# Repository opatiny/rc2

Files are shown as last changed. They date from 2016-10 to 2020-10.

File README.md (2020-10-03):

# Remote Control Cylinder

---
Link to "site": https://opatiny.github.io/rc2/.

__WARNING:__ This README is not the main source of information for this project. A detailled paper can be found [here](https://github.com/opatiny/rc2/blob/master/documentation/RemoteControlCylinder.pdf).

  

_Final cylinder prototype_

## Cite this repository

Océane Patiny, & Luc Patiny. (2020, October 3). opatiny/rc2: Remote controlled cylinder final documentation (Version v1.0.0). Zenodo. http://doi.org/10.5281/zenodo.4064763

## Abstract
This one year project consists in the development of a remote controlled cylinder that uses servo motors to displace its center of mass, which leads the cylinder to accelerate linearly. This implies that very diversified fields such as mathematics, physics, programming, electronics and mechanics had to be explored and partly understood to be combined in the final prototype. This prototype has an acrylic glass base structure with a diameter of 32 cm, it is controlled using a C.H.I.P. Pro (a micro-controller similar to Raspberry Pi) and a customized dedicated extension board. The board includes a driver for four servo motors and a 6 axis accelerometer. Finally, the power supply consists of a pack of three AA batteries. All the programming was made using JavaScript scripts that are run using Node.js and a Shell. In addition, the cylinder is remotely controlled through a web page, which make it easy and intuitive for the user. The final features of this robotic cylinder are the following: it can roll forwards and backwards, stop and keep itself balanced on a gentle slope . Also, it is only working well on flat, hard surfaces, though it could easily be adapted to rougher surfaces. The possibility has also been considered of creating a sphere that uses the same technologies as the cylinder that was constructed in this project. The results of the project can be seen easily in [this movie](https://youtu.be/QggOjoGjJhA).

## Liscence

Finally, this work is meant to be as open-source as possible. Therefore, the software that was developed is under MIT licence, whereas the hardware is under CERN OHL.

## Concept

Initially the project was inspired by a rover realized by [Octanis](https://www.octanis.org/), a student's association specialized in electronics. The rover was supposed to be send to Antarctica and be able to analyse it's environment autonomously. Seeing the Rover tested on a Glacier on a windy day made me wonder what would be the best design for a windproof robot and I immediately thought of a spherical robot. However, once I got back home and looked for similar ideas, I realized that they were already existing projects that consisted in a spherical robot. One of the most famous being the [Sphero](https://www.sphero.com/), a spherical robot toy.

Looking further, I also realized that most of the projects use a similar approach to move the sphere: I call it the hamster wheel approach. It basically is a little car which wheels lay on the outer, rigid shell that induces the movement. I, on the contrary, had imagined a completely different system: I would displace the center of mass of the cylinder to make it roll.

## Programming

All the code that allows the control of the cylinder is contained in the following repository:
[https://github.com/opatiny/rpi-cylinder](https://github.com/opatiny/rpi-cylinder).

The programming has been done in JavaScript (using Node.js) and HTML for the web page that allows the control of the cylinder. Websocket was used to make the web page dynamic.

## Documentation

You can find a lot mor documentation about this project in the [documentation](https://github.com/opatiny/rc2/tree/master/documentation) section of this repository. There, you will find pictures, a developed abstract, and the paper about this project.

## Videos

Cardboard model of the cylinder's mechanism: [https://youtu.be/4SuPhpwOK5g](https://youtu.be/4SuPhpwOK5g)

The mass of cylinderPrototype2 moving on a circle using an atMega32u4: [https://youtu.be/1zOCNZ_r5pY](https://youtu.be/1zOCNZ_r5pY)

Final cylinder's prototype presentation video:
[https://youtu.be/QggOjoGjJhA](https://youtu.be/QggOjoGjJhA)

## Repository structure

In this section, we explain what the different folders of this repository contain and what it was used for.

__Note:__ Three main prototypes were built during this project. To refer to them, we use the acronyms cp1, cp2 and cp3 ("cp" stands for "cylinderPrototype"). You can see pictures of the prototypes in the [Pictures section](#pictures).

### arduino
Very basic programs in Arduino that allowed to test the movement of the mass with cp2. The values of the angles of the servos motors depending on the mass position were exported from the [GeoGebra model](https://github.com/opatiny/rc2/blob/master/movingMassOnCircle/geogebra/cylinderPrototype2/cylinderPrototype2.ggb) that we designed.

### datasheets
Datasheets of the electronical components used in this project: servo motors (MG995), accelerometer (MPU6050), servos driver (PCA9685) and C.H.I.P..

### documentation
Main source of information about this project, contains a pdf of the paper, a presentation, posters and an abstract. You will also find pictures there.

### freecad
FreeCAD is the software we used to create the designs of the cylinder. The "exports" subfolder contains files that can be directly used to laser cut the different parts (.dxf).

### javascript
First JavaScript programs that implemented the mathematical formula that returns the angles of the servos depending on the position of the mass. This code is the base of the [chip](https://github.com/opatiny/chip) GitHub repository, which contains the final code.

### movingMassOnCircle
Contains the GeoGebra models of the cylinder's mass movement and files commenting the observations made based upon them.

### pcb
Contains the Eagle and KiCAD files of the extension boards. They are two different boards, because when working on the project after a year, I realized that the cylinder was no longer functionning. I therefore had to change the micro-controller, because C.H.I.P. had made bankrupt. I decided to switch to a Raspberry Pi Nano W.

### raspberry
Procedure allowing to format a Raspberry Pi to make it act as a WiFi rooter.

## Pictures

Here are a few pictures of the project.

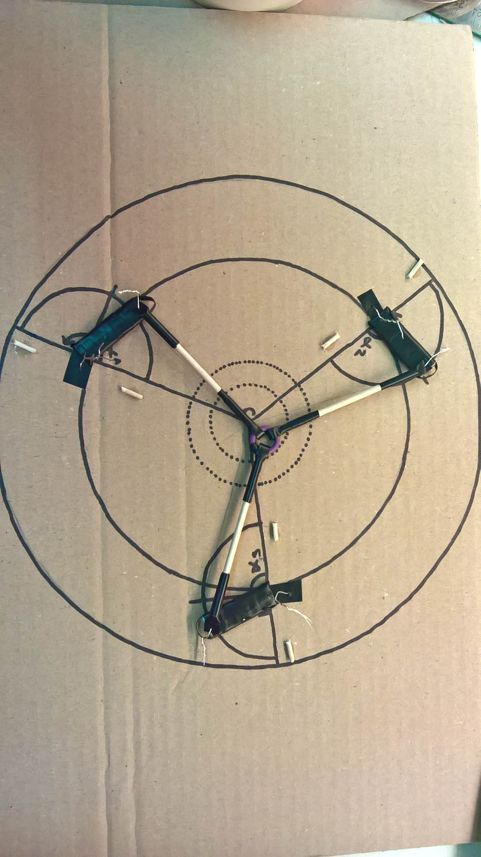
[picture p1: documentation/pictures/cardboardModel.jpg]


_Cardboard model of the cylinder_



_First prototype of the cylinder_

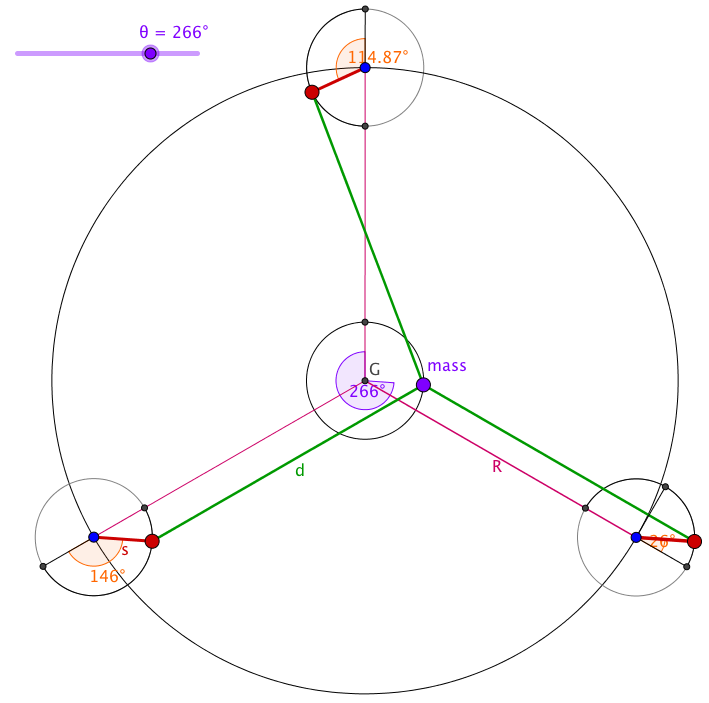
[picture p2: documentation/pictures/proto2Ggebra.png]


_[GeoGebra](https://www.geogebra.org/) model allowing to see the movement of the servo motors_



_Close-up of the second prototype_

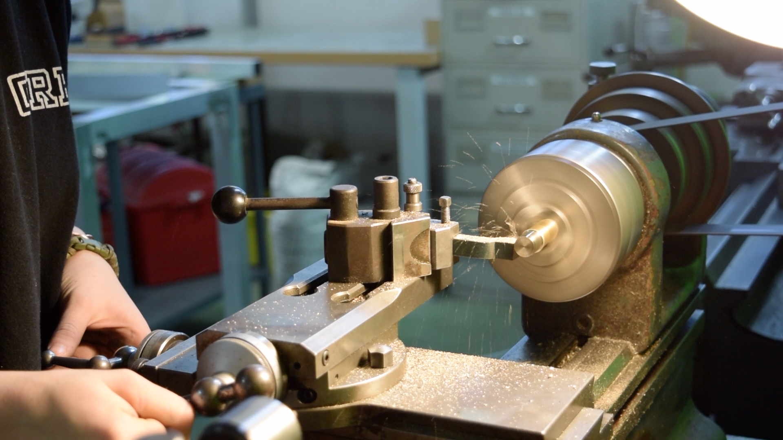
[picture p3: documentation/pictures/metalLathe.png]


_Metal turning a part of cp3_



_PCB extension allowing the connection of two I2C peripherals to the C.H.I.P. Pro (accelerometer and servo driver)_



_Long aperture picture of the mass moving on a spiral (cp3), max radius is 40mm_

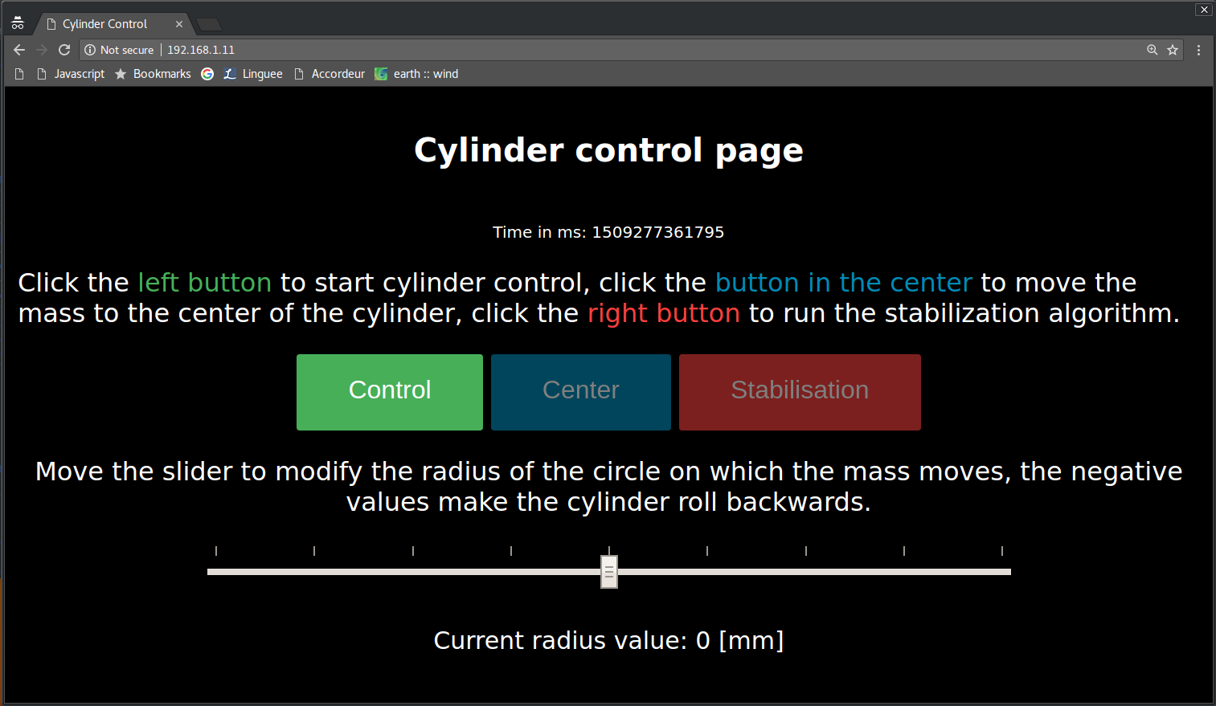
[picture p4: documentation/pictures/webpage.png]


_Final control web page_

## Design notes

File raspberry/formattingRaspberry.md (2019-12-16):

# How to format a Raspberry Pi and install various software
------

## Installing the OS (Raspbian)
First of all, you need an SD card that fits in the Raspberry Pi.

To achieve the installation, we follow the tutorial on this link: https://www.raspberrypi.org/documentation/installation/installing-images/linux.md

 - Go on https://www.raspberrypi.org/downloads/raspbian/ and download the "Raspbian Stretch Lite" as ZIP.

 - Use the `lsblk` command to see all disks
 - Insert your SD card in the computer
 - Run `lsblk` again. Your SD card is the device that just appeared. Check the size to be sure.
 - If the card is mounted somewhere (you see that in the rightmost column, blank means that the card is not mounted), unmount it using `umount`.
 - To copy the image to the SD card, run 

   `dd bs=4M if=2018-11-13-raspbian-stretch.img of=/dev/sdX status=progress conv=fsync`

   `if` is the input file, `of` is the output file. `status=progress` allows to see the progress of the copy operation.

   __CAUTION:__ don't make mistakes in the `of`, because you can overwrite your computer's hard drive.

## Logging in (default)
__username:__ pi  
__password:__ raspberry

## Enable SSH
 - `raspi-config`
 - 5 Interfacing Options
 - P2 SSH

 ## Enable WIFI hotspot
 https://www.raspberrypi.org/documentation/configuration/wireless/access-point.md

 These commands are supposed to work for Raspberry Pi 3 and Zero W.

 - `sudo apt-get install dnsmasq hostapd`
 - Then turn the new software off  
   `sudo systemctl stop dnsmasq`  
   `sudo systemctl stop hostapd`
 - Then reboot  
   `sudo reboot`
 - Edit the dhcpcd configuration file with:  
   `sudo nano /etc/dhcpcd.conf`
 - Add to the end of the file
   ```
    interface wlan0
      static ip_address=172.16.1.1/24
      nohook wpa_supplicant
   ```
 - restart the dhcpcd daemon and set up the new wlan0   configuration:  
  `sudo service dhcpcd restart`

### Configuring the DHCP server (dnsmasq)
- We are going to write a configuration file from scratch
- `sudo mv /etc/dnsmasq.conf /etc/dnsmasq.conf.orig`  
- Edit the file with  
  `sudo nano /etc/dnsmasq.conf`  
  and paste that in it
   ```
   interface=wlan0  # Use the require wireless interface - usually wlan0
     dhcp-range=172.16.1.100,172.16.1.200,255.255.255.0,24h
   ```

### Configuring access point host software (hostapd)
- We are going to write a configuration file from scratch 
- Edit the file with  
  `sudo nano /etc/hostapd/hostapd.conf`  
  and paste that in it
   ```
    interface=wlan0
    driver=nl80211
    ssid=CylinderControl
    hw_mode=g
    channel=7
    wmm_enabled=0
    macaddr_acl=0
    auth_algs=1
    ignore_broadcast_ssid=0
    wpa=2
    wpa_passphrase=CylinderControl
    wpa_key_mgmt=WPA-PSK
    wpa_pairwise=TKIP
    rsn_pairwise=CCMP
   ```
- Tell the system where to find the file:
  `sudo nano /etc/default/hostapd`
- Replace the line with `#DAEMON_CONF` and replace by
  `DAEMON_CONF="/etc/hostapd/hostapd.conf"`

### Starting it
- Turn these on again:  
   `sudo systemctl start dnsmasq`  
   `sudo systemctl start hostapd`
- To add masquerade and rooting, see tutorial
- Reboot
- Connect to the WiFi from a wireless device and try to ssh the Raspberry with  
  `ssh pi@172.16.1.1`

## Swap from WiFi hotspot to local network
It's quite quick, normally.

__Link:__ https://raspberrypihq.com/how-to-connect-your-raspberry-pi-to-wifi/

__Step 1:__ remove the three lines added at the end of `/etc/dhcpcd.conf`.

__Step 2:__ add the following lines at the end of `/etc/wpa_supplicant/wpa_supplicant.conf`.

```
  network={
    ssid="Wifi network name"
    psk="password"
  }
```

If necessary, reboot. Then, the device should appear on the list of devices connected to the WiFi rooter.

## Various installs
Run `apt-get update`

### GitHub
As root:  
`apt-get install git`

### Node.js and npm
You should not use apt-get because it is as old version.Instead, use nodesource
as root:  
```
apt-get install xz-utils
cd /usr/local/
wget https://nodejs.org/dist/v10.15.2/node-v10.15.2-linux-armv6l.tar.xz
unxz node-v10.15.2-linux-armv6l.tar.xz
tar -xvf node-v10.15.2-linux-armv6l.tar
rm node-v10.15.2-linux-armv6l.tar
ln -s /usr/local/node-v10.15.2-linux-armv6l/bin/node /usr/local/bin/node
ln -s /usr/local/node-v10.15.2-linux-armv6l/bin/npm /usr/local/bin/npm
ln -s /usr/local/node-v10.15.2-linux-armv6l/bin/npx /usr/local/bin/npx
```

### I2C
To enable I2C and serial and access to other paramters, use the `raspi-config` command.

Packages to manage I2C:  
`sudo apt-get install python-sm bus`  
`sudo apt-get install i2c-tools`

To scan the I2C bus:  
`i2cdetect -y 1`

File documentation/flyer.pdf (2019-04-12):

# REMOTE CONTROL

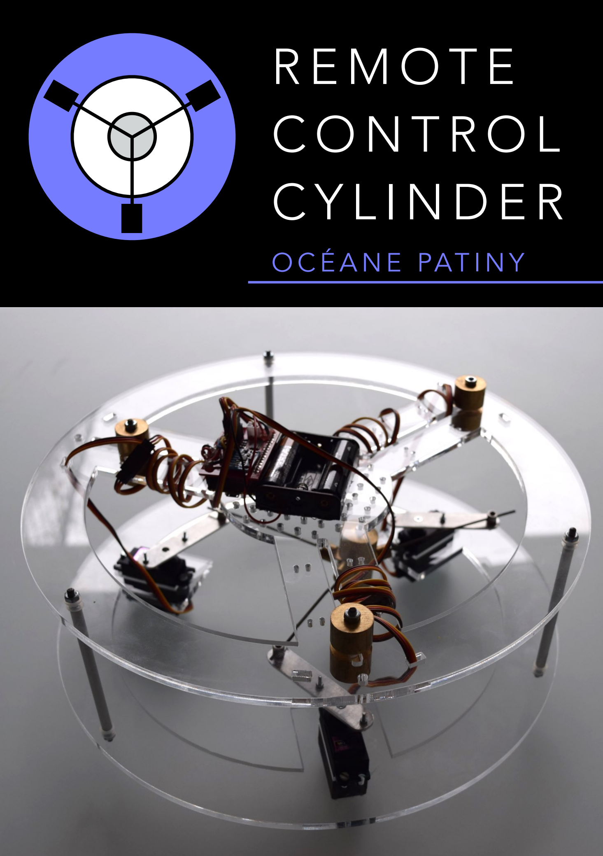
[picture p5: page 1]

# CYLINDER

### OCÉANE PATINY

This open-source project consists in the development of a remote controlled cylinder that uses servo motors to displace a mass in its center, which causes the cylinder to move. The final prototype that was built has a PMMAbased structure with a diameter of 32 cm. It is controlled using a C.H.I.P. Pro microcontroller and a dedicated board extension. The board includes two I2C slaves: a driver for four servo motors and a 6-axis IMU. Finally, the power supply is assured by a pack of three AA batteries. All the programming was made using JavaScript. The cylinder can be controlled remotely and can roll forwards and backwards, stop and keep itself balanced on a gentle slope. In addition, to make the control of the prototype easier, a web page was coded, which includes buttons and sliders. The movement characteristics of the cylinder have also been studied. This kind of design opens the doors to new types of vehicles with cylindrical or spherical wheels

## REMOTE CONTROL CYLINDER

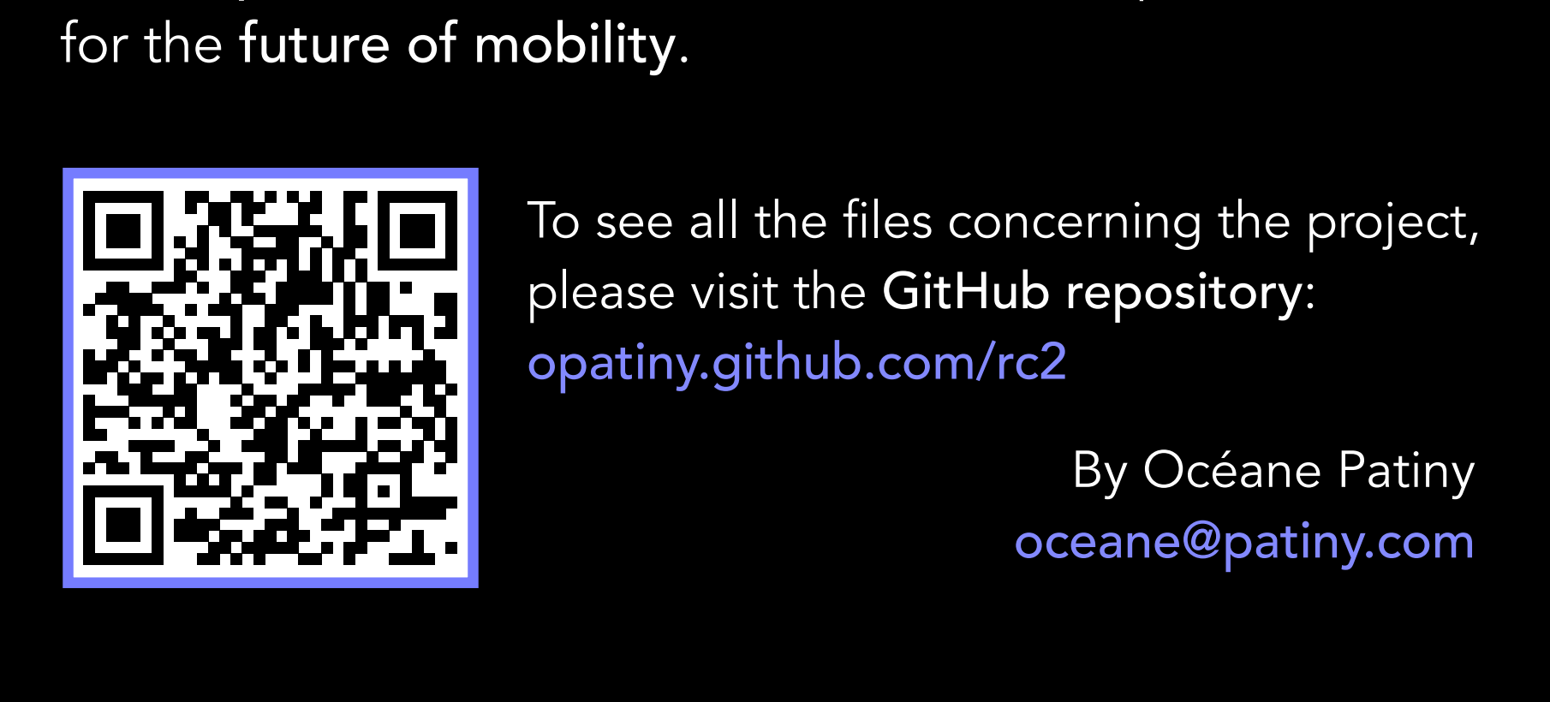
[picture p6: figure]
for the future of mobility.; By Océane Patiny oceane@patiny.com; please visit the GitHub repository: opatiny.github.com/rc2

To see all the files concerning the project,

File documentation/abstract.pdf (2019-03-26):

## Océane Patiny

# Remote control cylinder

### Abstract

This project consists in the development of a remote controlled cylinder that uses servo motors to displace a mass in its center, which causes the cylinder to move . The final prototype that was built has a PMMA-based structure with a diameter of 32 cm. It is controlled using a C.H.I.P. Pro microcontroller and a dedicated board extension. The board includes two I2C slaves: a driver for four servo motors and a 6-axis IMU. Finally, the power supply is assured by a pack of three AA batteries. All the programming was made using JavaScript. The cylinder can be controlled remotely and can roll forwards and backwards, stop and keep itself balanced on a gentle slope. In addition, to make the control of the prototype easier, a web page was coded, which includes buttons and sliders. The movement characteristics of the cylinder have also been studied. This kind of design opens the doors to new types of vehicles with cylindrical or spherical wheels for the future of mobility.

### Introduction

In the last twenty years, research in the field of spherical robots has been actively undertaken. The results, though, nearly always put forward an approach in which there is an internal drive mechanism, whose wheels lay on an outer, rigid shell. Here, we wanted to explore other possibilities to induce movement to a sphere. Yet, due to time and means restrictions, we had to focus on the 2D version: a cylinder.
The goal was therefore to achieve designing and building a remotely controlled cylinder that rolls when its center of mass is displaced using a technology that could be adapted to a sphere. It was also important to achieve that independently from any institution and to allow all the results to be open-source, so that anyone keen to remake what was done during the project could do so.

### Methods

First of all, various approaches have been investigated, but it has quickly been realised that the most feasible solution was to use three servo motors placed on an equilateral triangle outside the cylinder and to connect them to a mass in the center with rigid bars. Once the approach was chosen, we had to find a mathematical formula that links the position of the mass in the center to the angles of the servo motors. Then, preliminary prototypes were built. We had access to a laser cutter to cut the base structure for the cylinder. This allowed to run first tests with basic arduino programs, which showed that the chosen approach was working. This led to the development of a dedicated PCB extension that would act as a shield on the microcontroller we chose: a C.H.I.P. Pro. The final phase was writing the code and debugging, which was done in JavaScript.

Also, the software that was developed is under MIT licence, whereas the hardware is under CERN OHL.

### Results

The final prototype we built shows that the technology that we adopted works very well to make a cylinder roll. The features that we managed to obtain are for the cylinder to roll backwards and forwards at different speeds (with a maximum speed of 1.03 m/s), stop and remain balanced on a gentle slope (max. 3°). However, the cylinder works the best on hard and flat surfaces. The last prototype has an acrylic glass base structure, a diameter of 32 cm and weights ~1380 g. The power supply consists of a pack of three AA batteries, which gives it a theoretical autonomy of ~9.8 hours in standby and ~3.7 hours rolling. The control of the cylinder is done through a web page and is therefore easy and intuitive for anyone.

### Discussion

In general, the results are really satisfying, because they prove the efficiency of the method that we invented. Also, they are several advantages that this approach provides, compared to the one generally used in spherical robots, which is placing a little car inside it. First of all, the mass that we move can be placed exactly in the center of the sphere, which allows it to roll freely, nearly without any energy costs. In addition, the whole sphere would only be made of one part, since all the components are connected together. So, the relative position between the outer shell is always known, because it is not possible for the shell to slip under the wheels of the drive mechanism, like in a standard approach.

### Conclusions

We have theoretically and practically shown that it is possible to use three servo motors to displace a mass in the center of a cylinder and therefore generate motion. If the project was to be continued, it would be highly interesting to build a sphere working on the same principle.

### SURPLUS

This implies that very diverse fields such as mathematics, physics, programming, electronics and mechanics had to be explored and partly understood to be combined in the final prototype.

Often, pop culture and science-fiction in particular reflect the interest of a society for a certain subject. In the last 50 years, they have been various cases of spheres that can move in an autonomous way in movies and TV series. An easy example is BB-8, a robot with a spherical body that appeared on screen for the first time in 2015, in The Force Awakens (Star Wars).

Since this project required designing, modeling and building, it is very interdisciplinary. To realise this project, knowledge from five different fields had to be acquired. These fields are mathematics, physics, mechanics, electronics and programming.

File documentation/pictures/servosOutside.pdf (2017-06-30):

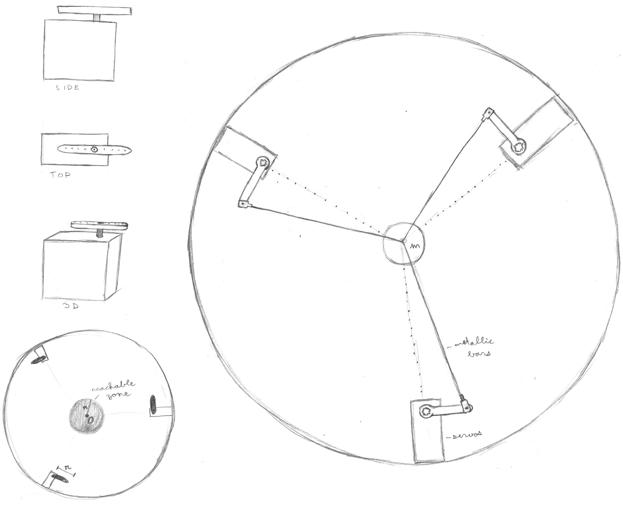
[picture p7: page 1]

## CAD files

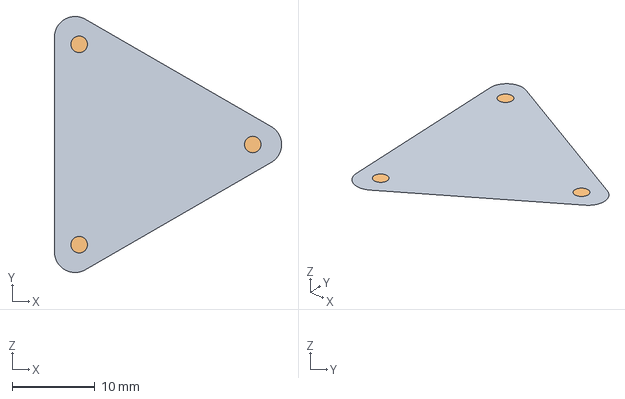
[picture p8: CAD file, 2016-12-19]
freecad/centerMass/mass.fcstd
27.5 x 31.0 x 0 mm
triangle

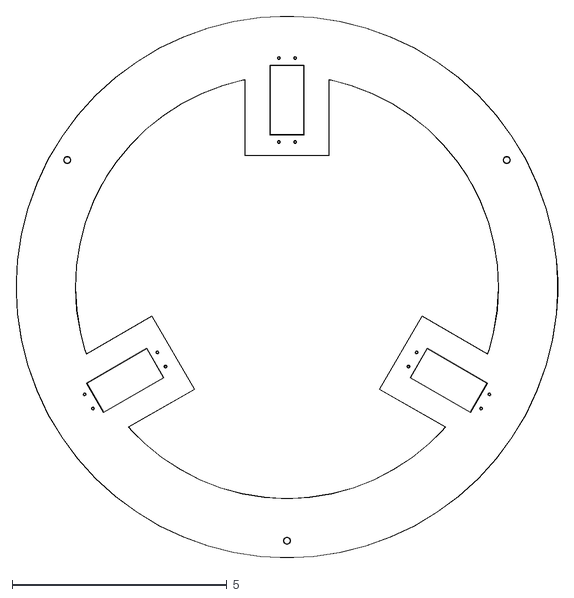
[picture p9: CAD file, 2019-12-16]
freecad/exports/cylinderPrototype3F.dxf
12.6 x 12.6

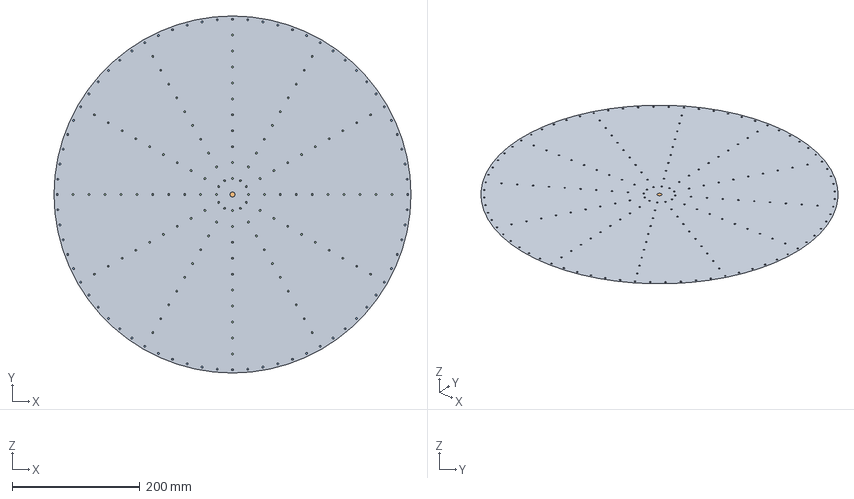
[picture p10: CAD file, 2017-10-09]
freecad/wheel/Wheel.fcstd
560.0 x 560.0 x 0 mm
externalCircle
centerHole
extArray
intArray

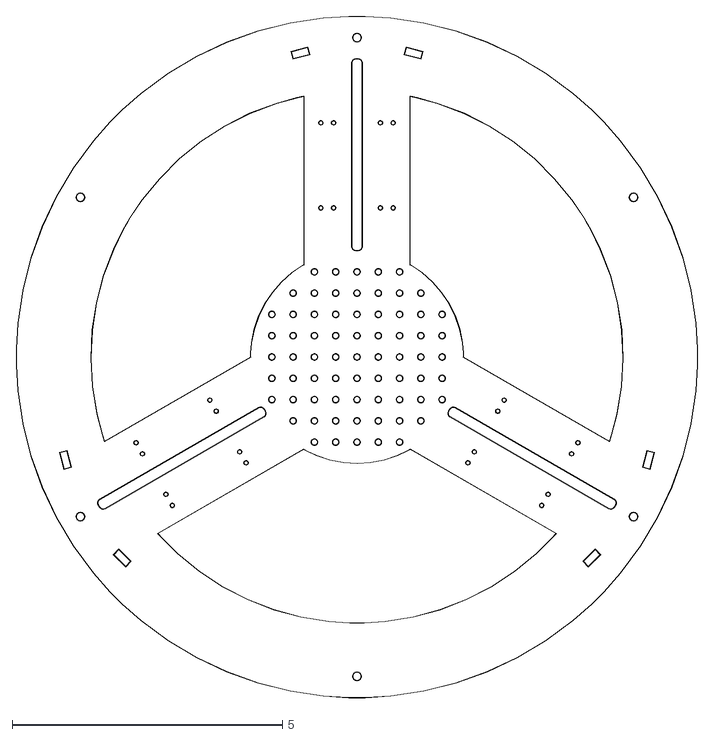
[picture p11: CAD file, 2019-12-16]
freecad/exports/cylinderPrototype3B.dxf
12.6 x 12.6

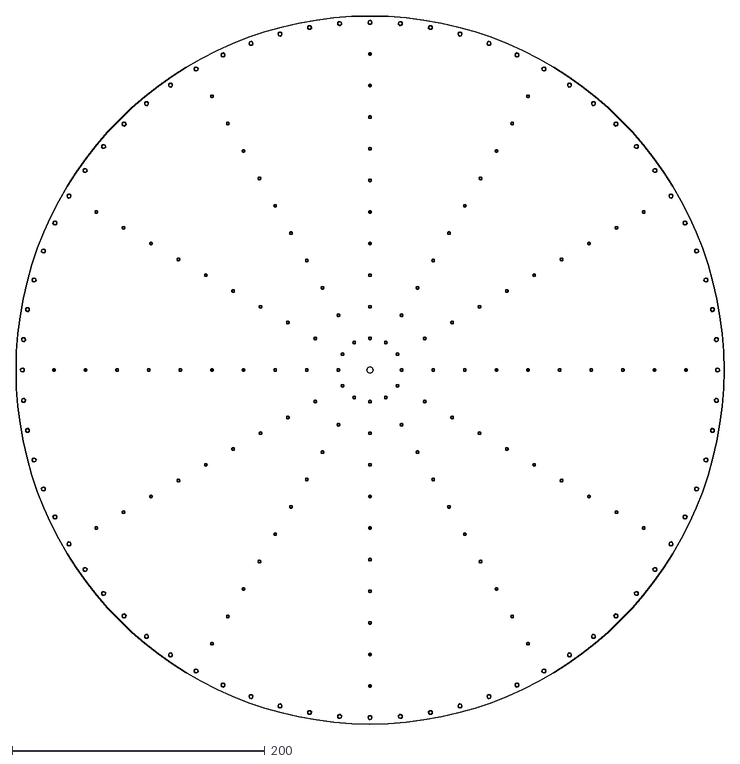
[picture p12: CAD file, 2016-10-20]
freecad/exports/wheel.dxf
560.0 x 560.0

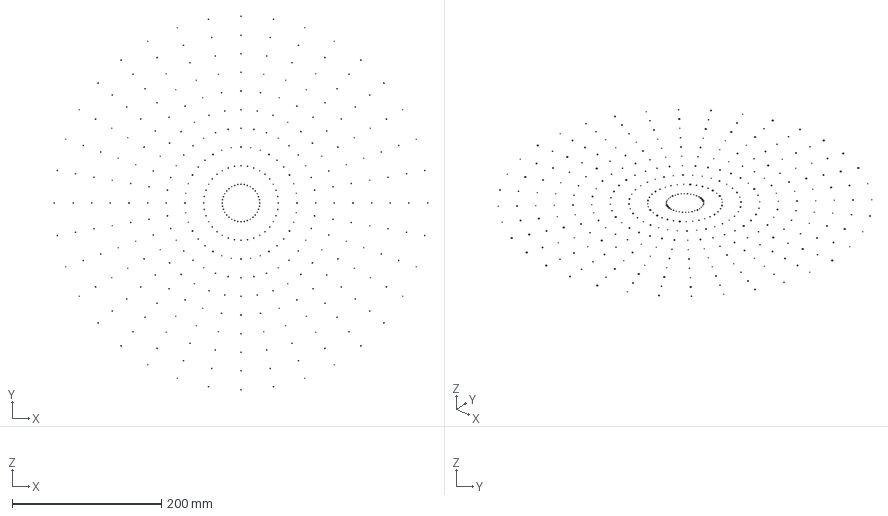
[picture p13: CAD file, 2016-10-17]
freecad/wheel/wheelTest.fcstd
501.0 x 501.0 x 0 mm

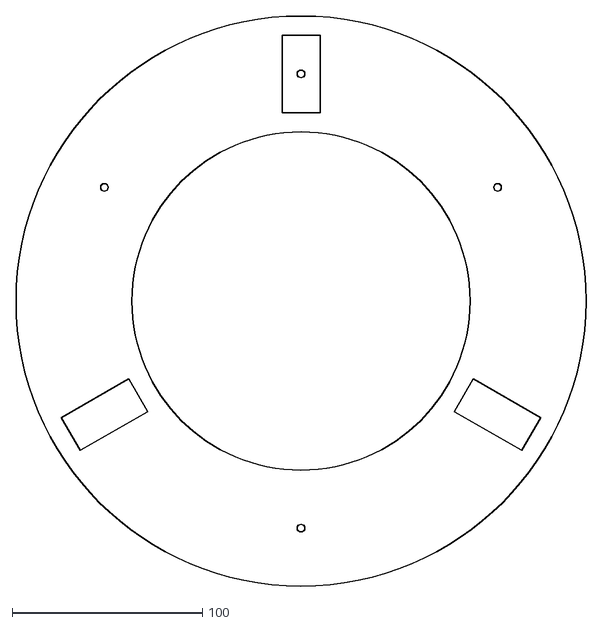
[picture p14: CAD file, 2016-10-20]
freecad/exports/model-cylinder.dxf
300.0 x 300.0

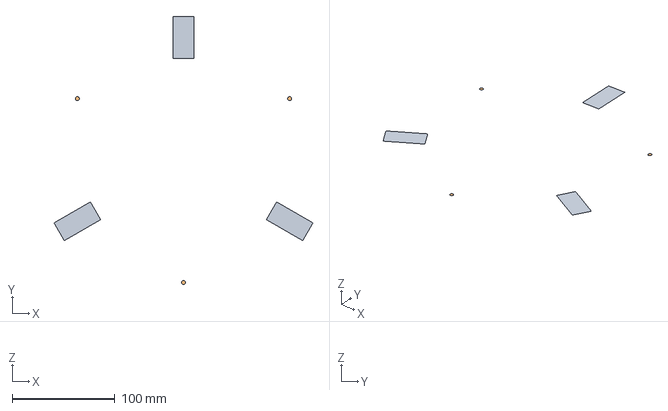
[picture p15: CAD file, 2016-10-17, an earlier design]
freecad/cylinderPrototype2/cylinder.fcstd
252.5 x 261.5 x 0 mm
servoArray
screwArray

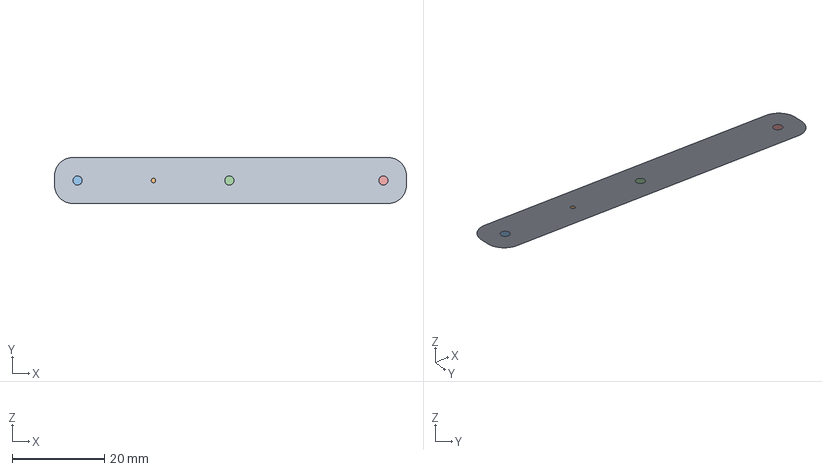
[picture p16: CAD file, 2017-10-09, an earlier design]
freecad/cylinderPrototype3/servoAxis.fcstd
76.5 x 10.0 x 0 mm
Rectangle
Circle
axisHole
axisHole2
axisHole3

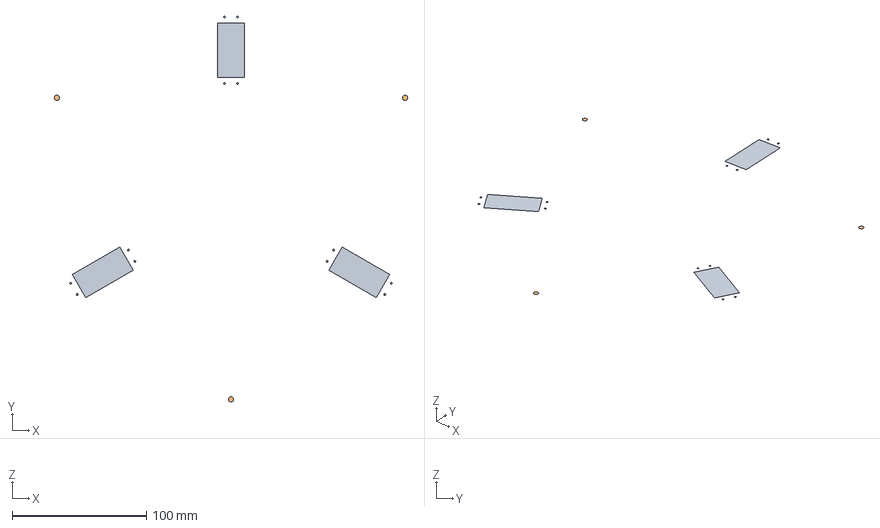
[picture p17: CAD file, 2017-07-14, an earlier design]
freecad/cylinderPrototype3/cylinderServoFace.fcstd
263.8 x 288.0 x 0 mm
servoArray
screwArray
arrayOfHoleServo

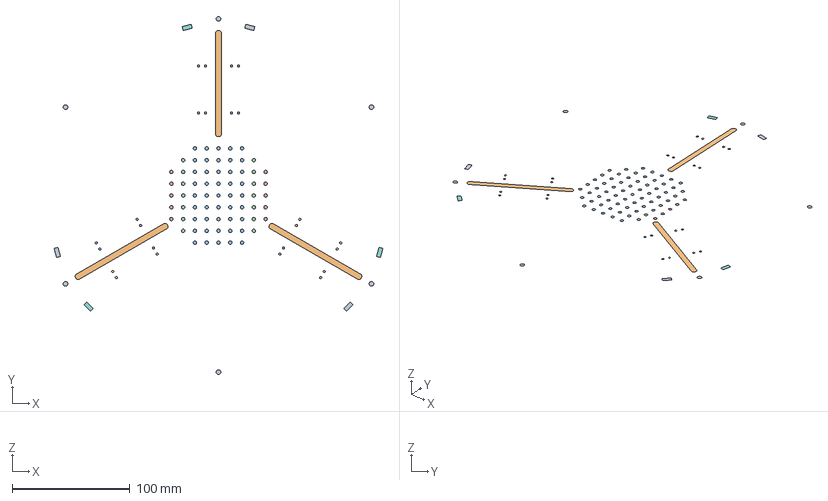
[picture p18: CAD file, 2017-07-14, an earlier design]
freecad/cylinderPrototype3/cylinderBackFace.fcstd
279.2 x 304.0 x 0 mm
screwArray
slitArray
innerHoleArray1
innerHoleArray2
innerHoleArray3
middleHoleArray1
middleHoleArray2
rectangleArray1
rectangleArray2

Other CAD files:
freecad/cylinder/test.FCStd
freecad/wheel/wheelBase.FCStd
freecad/wheel/Wheel.dxf

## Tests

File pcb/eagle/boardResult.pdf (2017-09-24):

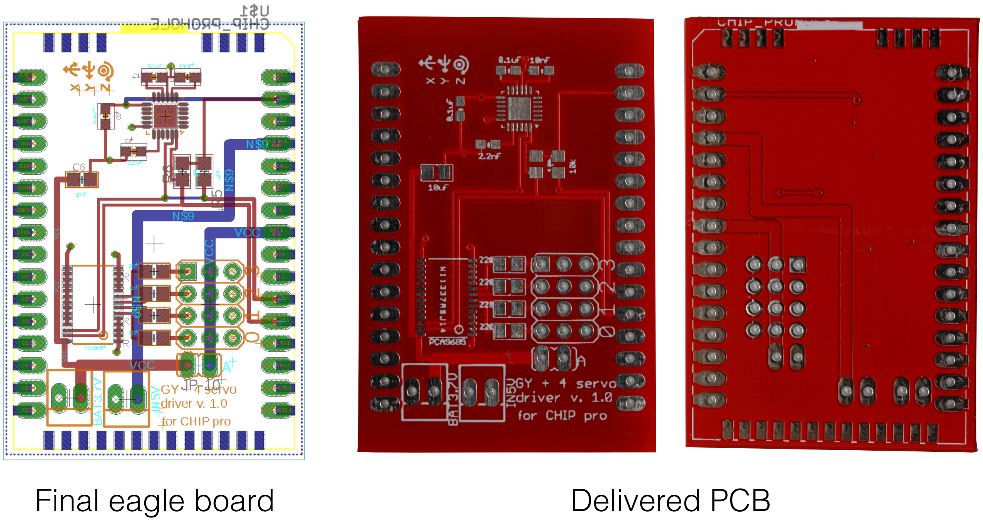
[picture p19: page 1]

Final eagle board | Delivered PCB

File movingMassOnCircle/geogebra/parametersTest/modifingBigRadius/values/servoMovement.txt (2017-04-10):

theta	alpha1
0.00000000000000	0.00000000000000
1.00000000000000	1.00000000000000
2.00000000000000	2.00000000000000
3.00000000000000	3.00000000000000
4.00000000000000	4.00000000000000
5.00000000000000	5.00000000000000
6.00000000000000	6.00000000000000
7.00000000000000	7.00000000000000
8.00000000000000	8.00000000000000
9.00000000000000	9.00000000000000
10.0000000000000	10.0000000000000
11.0000000000000	11.0000000000000
12.0000000000000	12.0000000000000
13.0000000000000	13.0000000000000
14.0000000000000	14.0000000000000
15.0000000000000	15.0000000000000
16.0000000000000	16.0000000000000
17.0000000000000	17.0000000000000
18.0000000000000	18.0000000000000
19.0000000000000	19.0000000000000
20.0000000000000	20.0000000000000
21.0000000000000	21.0000000000000
22.0000000000000	22.0000000000000
23.0000000000000	23.0000000000000
24.0000000000000	24.0000000000000
25.0000000000000	25.0000000000000
26.0000000000000	26.0000000000000
27.0000000000000	27.0000000000000
28.0000000000000	28.0000000000000
29.0000000000000	29.0000000000000
30.0000000000000	30.0000000000000
31.0000000000000	31.0000000000000
32.0000000000000	32.0000000000000
33.0000000000000	33.0000000000000
34.0000000000000	34.0000000000000
35.0000000000000	35.0000000000000
36.0000000000000	36.0000000000000
37.0000000000000	37.0000000000000
38.0000000000000	38.0000000000000
39.0000000000000	39.0000000000000
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

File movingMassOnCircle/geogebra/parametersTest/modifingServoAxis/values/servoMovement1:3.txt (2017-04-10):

theta	alpha1
0.00000000000000	79.2297293000036
1.00000000000000	79.1233790556336
2.00000000000000	79.0240489981939
3.00000000000000	78.9317780709813
4.00000000000000	78.8466009554279
5.00000000000000	78.7685480558326
6.00000000000000	78.6976454915653
7.00000000000000	78.6339150966937
8.00000000000000	78.5773744269494
9.00000000000000	78.5280367739248
10.0000000000000	78.4859111863639
11.0000000000000	78.4510024983763
12.0000000000000	78.4233113643898
13.0000000000000	78.4028343006216
14.0000000000000	78.3895637328329
15.0000000000000	78.3834880501080
16.0000000000000	78.3845916643807
17.0000000000000	78.3928550754136
18.0000000000000	78.4082549409238
19.0000000000000	78.4307641515316
20.0000000000000	78.4603519102012
21.0000000000000	78.4969838158346
22.0000000000000	78.5406219506696
23.0000000000000	78.5912249711331
24.0000000000000	78.6487482017965
25.0000000000000	78.7131437320788
26.0000000000000	78.7843605153473
27.0000000000000	78.8623444700644
28.0000000000000	78.9470385826421
29.0000000000000	79.0383830116611
30.0000000000000	79.1363151931314
31.0000000000000	79.2407699464704
32.0000000000000	79.3516795808925
33.0000000000000	79.4689740019119
34.0000000000000	79.5925808176724
35.0000000000000	79.7224254448341
36.0000000000000	79.8584312137604
37.0000000000000	80.0005194727590
38.0000000000000	80.1486096911520
39.0000000000000	80.3026195609607
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

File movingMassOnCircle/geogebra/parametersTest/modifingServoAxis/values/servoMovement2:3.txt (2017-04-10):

theta	alpha1
0.00000000000000	55.6787712190177
1.00000000000000	55.4426061235113
2.00000000000000	55.2277923374535
3.00000000000000	55.0344164540897
4.00000000000000	54.8625296050252
5.00000000000000	54.7121478231891
6.00000000000000	54.5832526207520
7.00000000000000	54.4757917715917
8.00000000000000	54.3896802852336
9.00000000000000	54.3248015568366
10.0000000000000	54.2810086758366
11.0000000000000	54.2581258743362
12.0000000000000	54.2559500952179
13.0000000000000	54.2742526593086
14.0000000000000	54.3127810106951
15.0000000000000	54.3712605194623
16.0000000000000	54.4493963216868
17.0000000000000	54.5468751773808
18.0000000000000	54.6633673282532
19.0000000000000	54.7985283385250
20.0000000000000	54.9520009036032
21.0000000000000	55.1234166130809
22.0000000000000	55.3123976562925
23.0000000000000	55.5185584604100
24.0000000000000	55.7415072528250
25.0000000000000	55.9808475412529
26.0000000000000	56.2361795066232
27.0000000000000	56.5071013053180
28.0000000000000	56.7932102787108
29.0000000000000	57.0941040692210
30.0000000000000	57.4093816431927
31.0000000000000	57.7386442218929
32.0000000000000	58.0814961227403
33.0000000000000	58.4375455135688
34.0000000000000	58.8064050832945
35.0000000000000	59.1876926327900
36.0000000000000	59.5810315901051
37.0000000000000	59.9860514543994
38.0000000000000	60.4023881730952
39.0000000000000	60.8296844568325
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

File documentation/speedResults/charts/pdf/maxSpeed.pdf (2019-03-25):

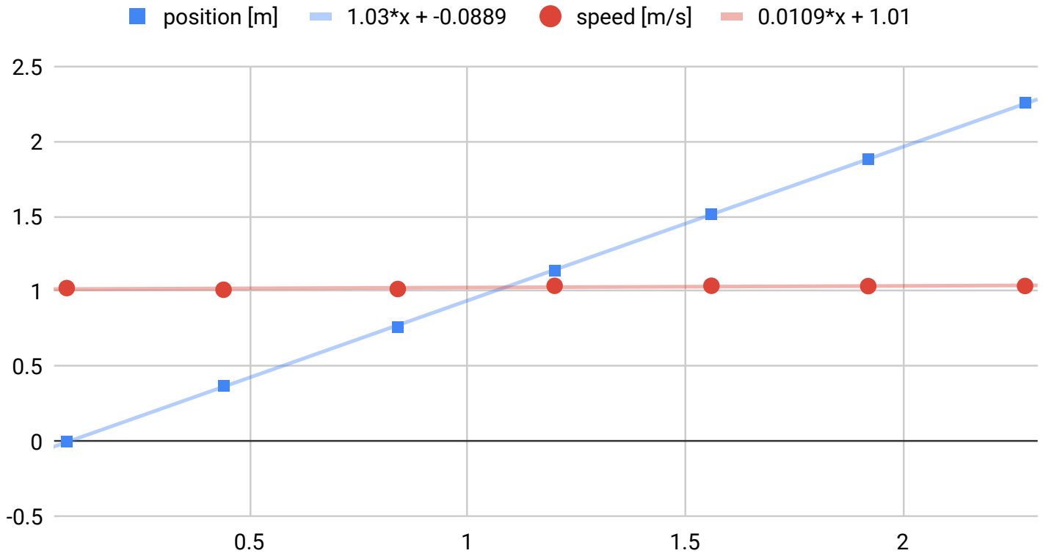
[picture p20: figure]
position [m]; speed [m/s]

time [s]

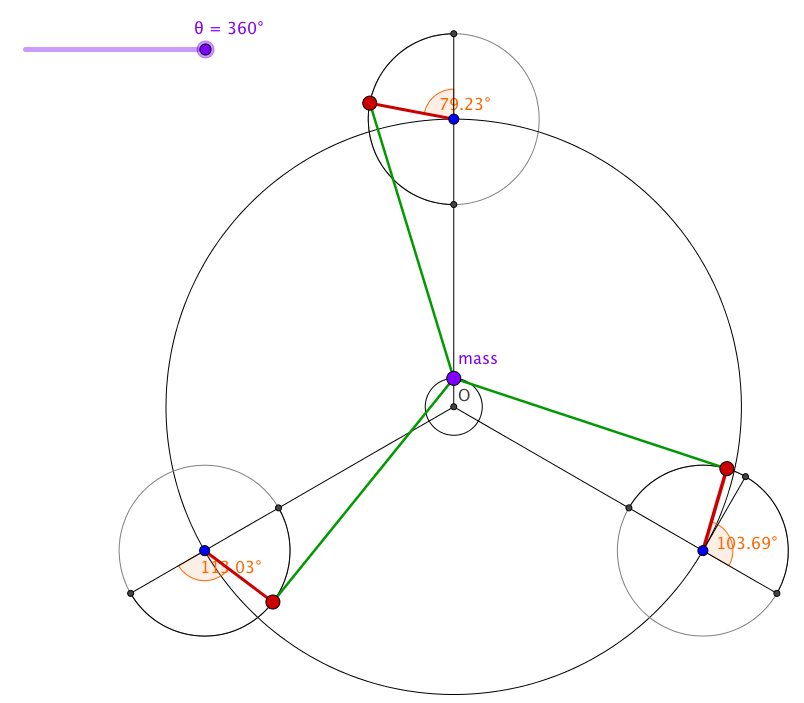
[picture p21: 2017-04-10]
movingMassOnCircle/geogebra/parametersTest/modifingServoAxis/pictures/servoMovement1:3.png

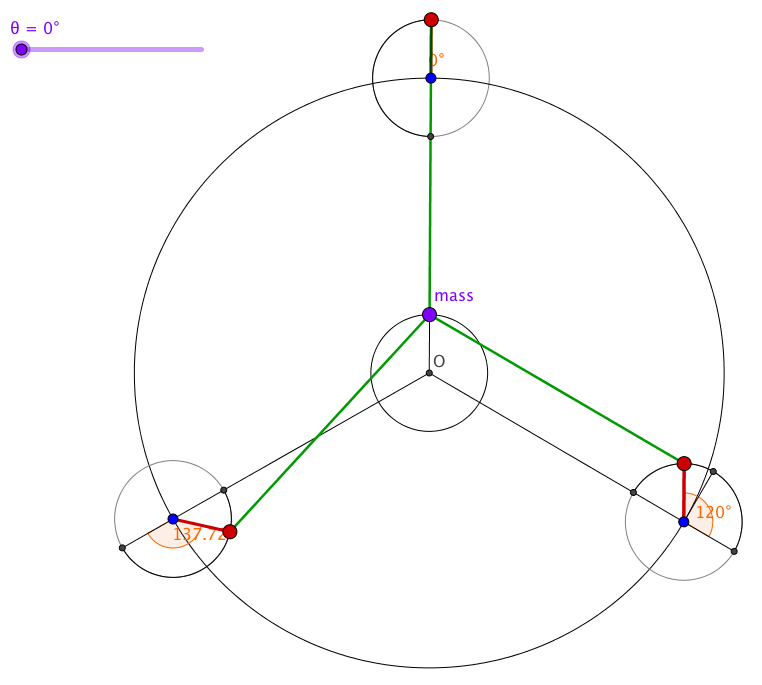
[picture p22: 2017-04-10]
movingMassOnCircle/geogebra/parametersTest/modifingBigRadius/pictures/servoMovement3:2.png

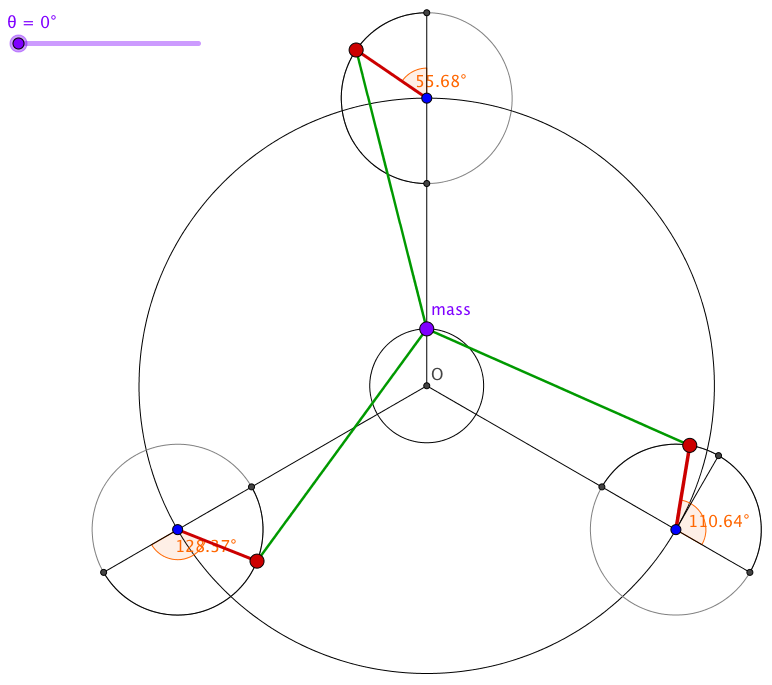
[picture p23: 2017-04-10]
movingMassOnCircle/geogebra/parametersTest/modifingServoAxis/pictures/servoMovement2:3.png

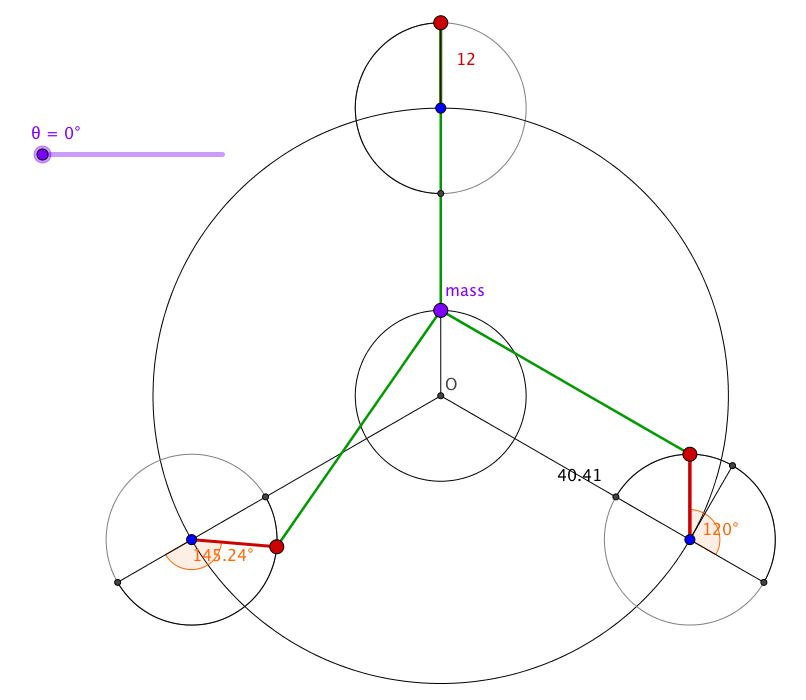
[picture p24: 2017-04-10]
movingMassOnCircle/geogebra/parametersTest/modifingServoAxis/pictures/servoMovement.png

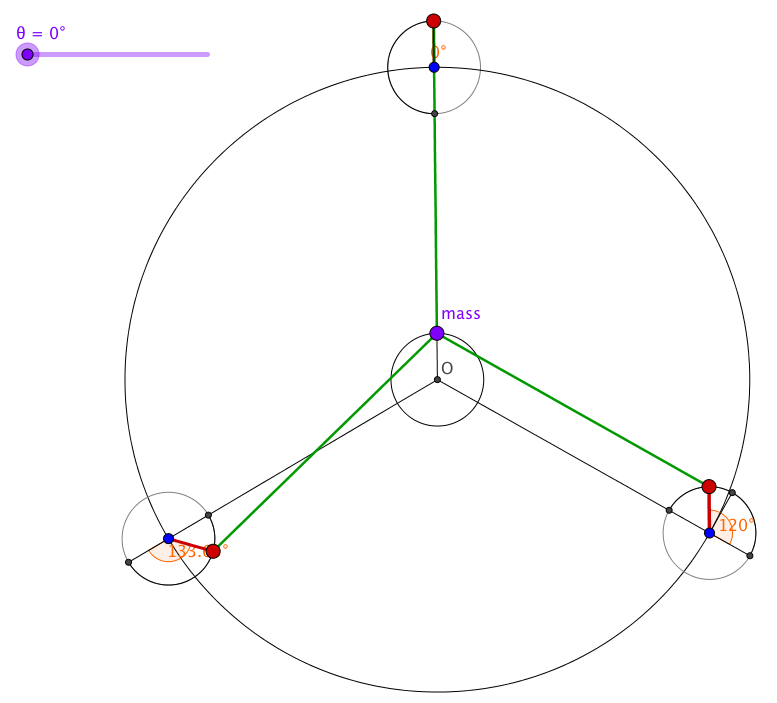
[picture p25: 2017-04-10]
movingMassOnCircle/geogebra/parametersTest/modifingBigRadius/pictures/servoMovement2.png

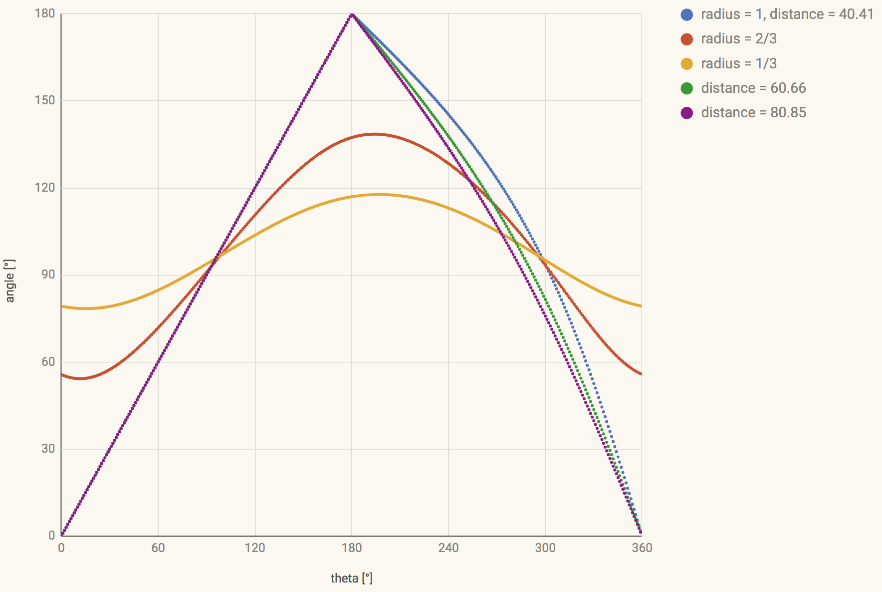
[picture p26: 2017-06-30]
movingMassOnCircle/graphs/firstGraphsVersion/parametersTest.png

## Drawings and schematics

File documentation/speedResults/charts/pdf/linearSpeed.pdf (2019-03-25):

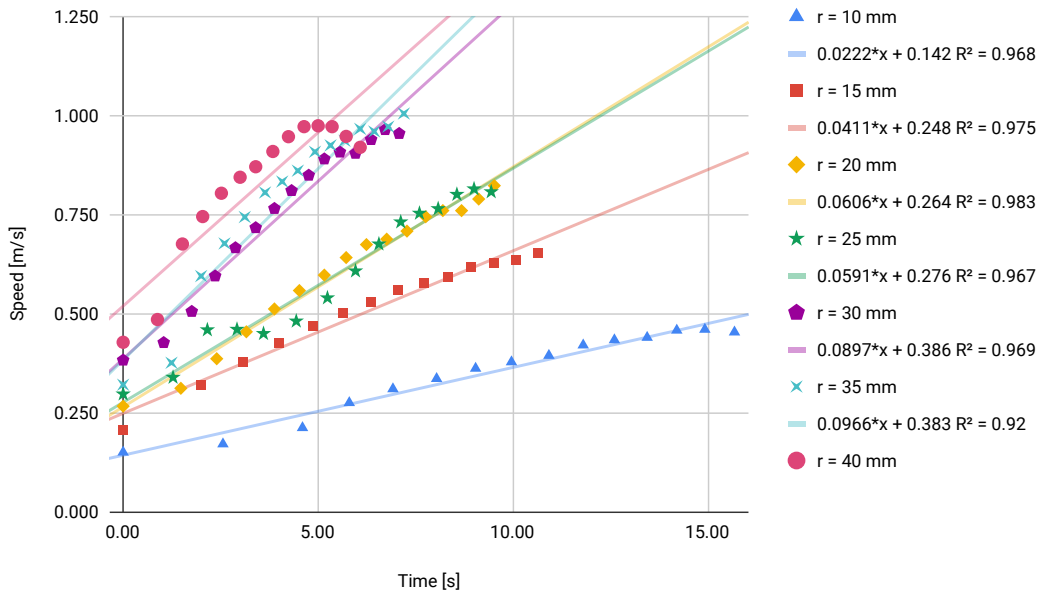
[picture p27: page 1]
Time [s]; Speed [m/s]

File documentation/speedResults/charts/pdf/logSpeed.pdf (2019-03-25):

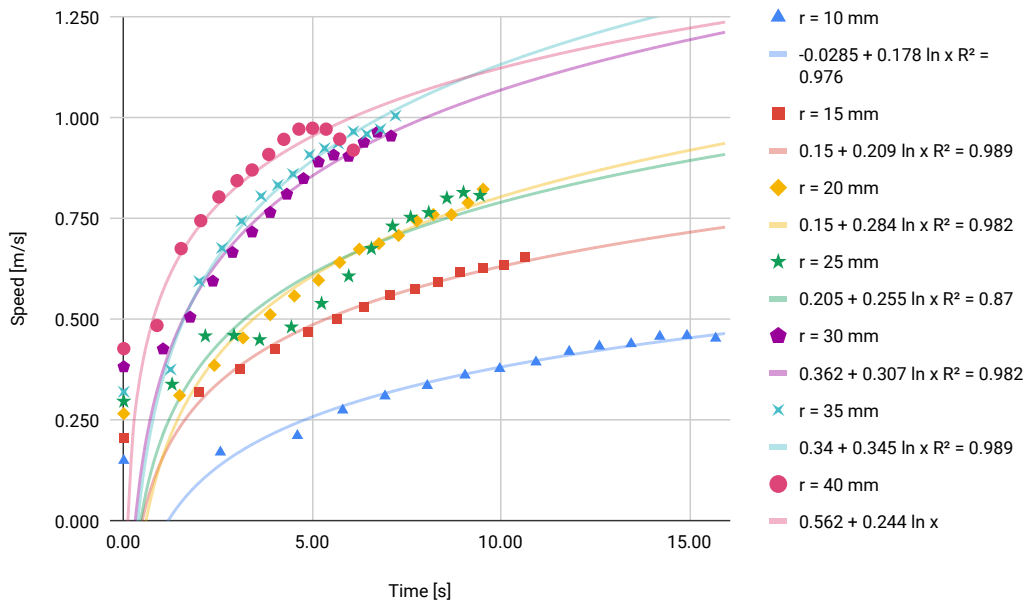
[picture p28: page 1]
Time [s]; Speed [m/s]

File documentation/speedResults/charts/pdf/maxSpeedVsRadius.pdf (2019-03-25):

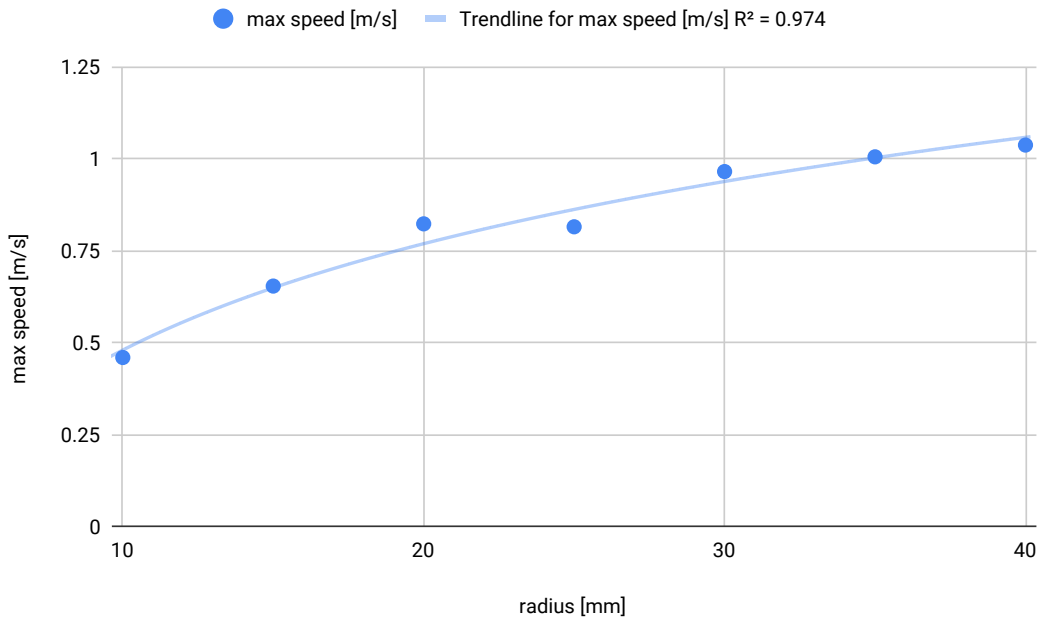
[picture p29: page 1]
radius [mm]; max speed [m/s]; Trendline for max speed [m/s] R² = 0.974

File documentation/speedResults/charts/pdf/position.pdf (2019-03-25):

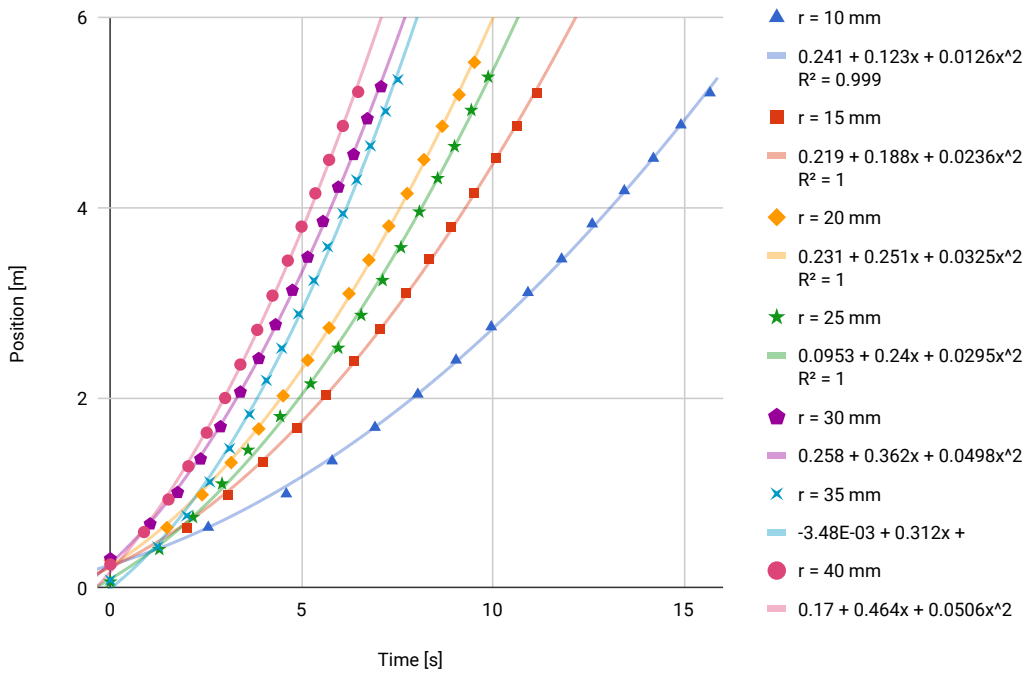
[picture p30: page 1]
Time [s]; Position [m]

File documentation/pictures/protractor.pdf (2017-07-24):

90

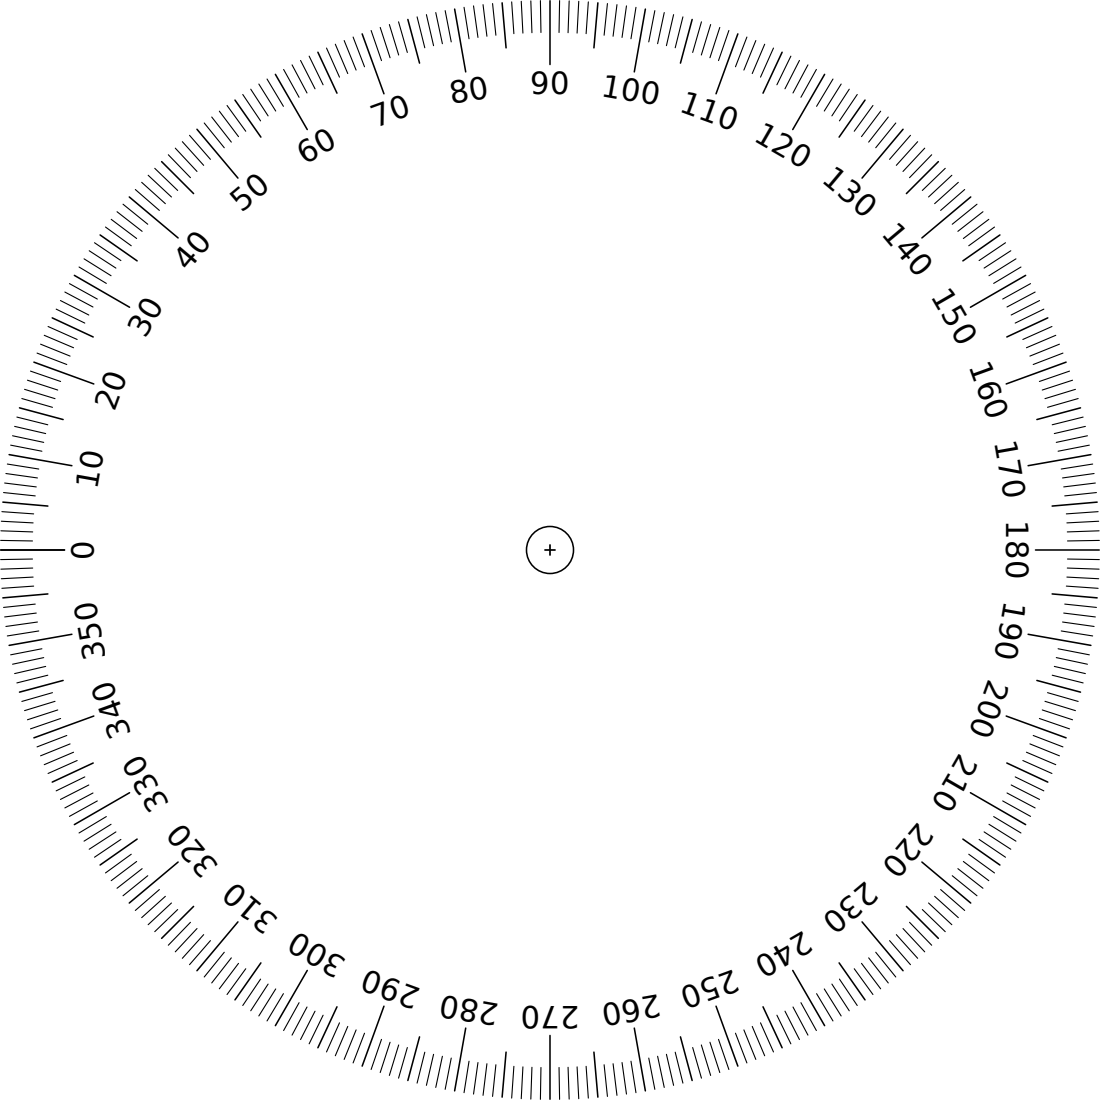
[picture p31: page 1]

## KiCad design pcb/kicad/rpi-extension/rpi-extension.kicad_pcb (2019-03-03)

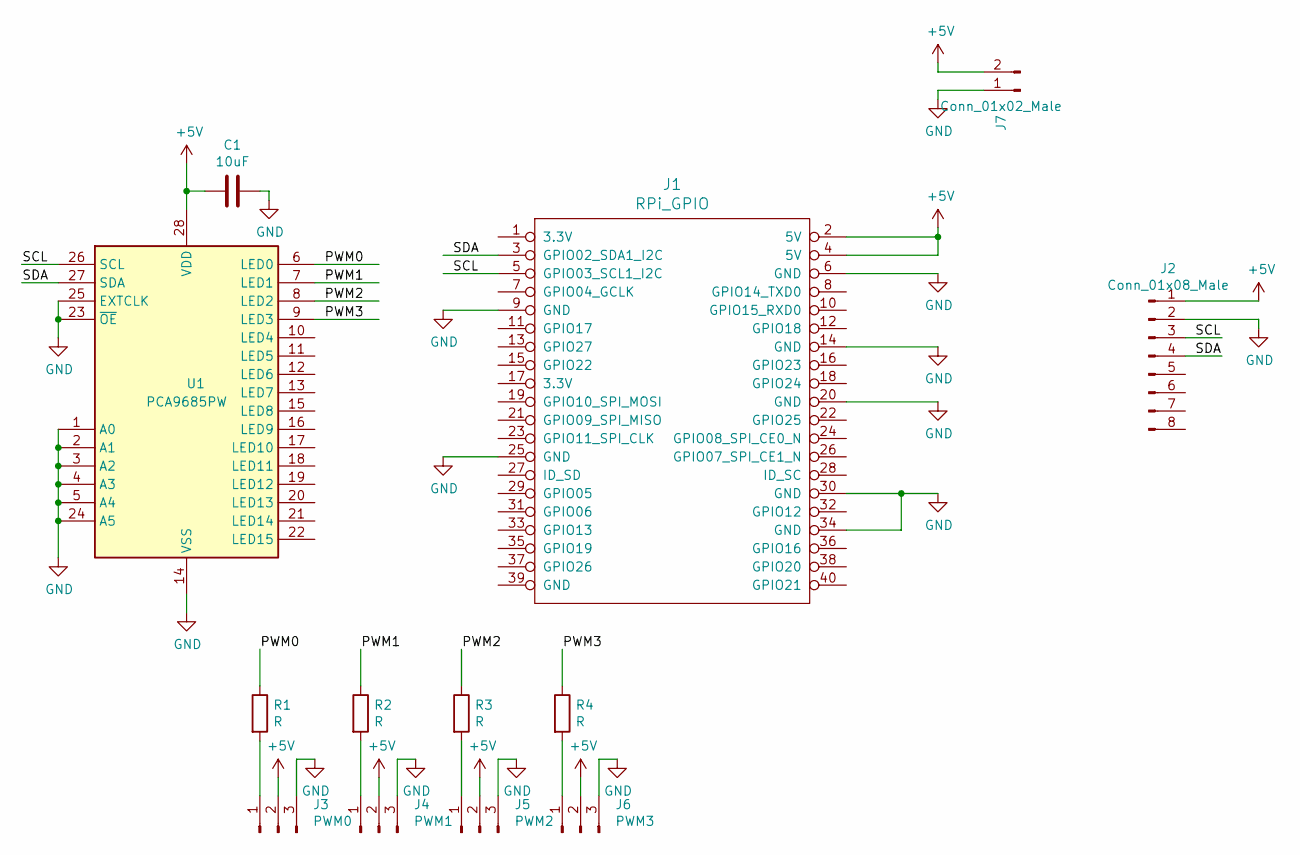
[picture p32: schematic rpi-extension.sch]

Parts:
C1: 10uF; C_0805_2012Metric_Pad1.15x1.40mm_HandSolder
J1: RPi_GPIO; PinSocket_2x20_P2.54mm_Vertical
J2: Conn_01x08_Male; PinHeader_1x08_P2.54mm_Vertical
J3: PWM0; PinHeader_1x03_P2.54mm_Vertical
J4: PWM1; PinHeader_1x03_P2.54mm_Vertical
J5: PWM2; PinHeader_1x03_P2.54mm_Vertical
J6: PWM3; PinHeader_1x03_P2.54mm_Vertical
J7: Conn_01x02_Male; Molex_KK-254_AE-6410-02A_1x02_P2.54mm_Vertical
R1, R2, R3, R4: R; R_0805_2012Metric_Pad1.15x1.40mm_HandSolder
U1: PCA9685PW; TSSOP-28_4.4x9.7mm_P0.65mm

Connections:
+5V: C1.2, J1.2 (5V), J1.4 (5V), J2.1, J3.2, J4.2, J5.2, J6.2, J7.2, U1.28 (VDD)
/PWM0: R1.1, U1.6 (LED0)
/PWM1: R2.1, U1.7 (LED1)
/PWM2: R3.1, U1.8 (LED2)
/PWM3: R4.1, U1.9 (LED3)
/SCL: J1.5 (GPIO03_SCL1_I2C), J2.3, U1.26 (SCL)
/SDA: J1.3 (GPIO02_SDA1_I2C), J2.4, U1.27 (SDA)
GND: C1.1, J1.6 (GND), J1.9 (GND), J1.14 (GND), J1.20 (GND), J1.25 (GND), J1.30 (GND), J1.34 (GND), J2.2, J3.3, J4.3, J5.3, J6.3, J7.1, U1.1 (A0), U1.2 (A1), U1.3 (A2), U1.4 (A3), U1.5 (A4), U1.14 (VSS), U1.23 (~OE), U1.24 (A5), U1.25 (EXTCLK)
unnamed: J3.1, R1.2
unnamed: J4.1, R2.2
unnamed: J5.1, R3.2
unnamed: J6.1, R4.2

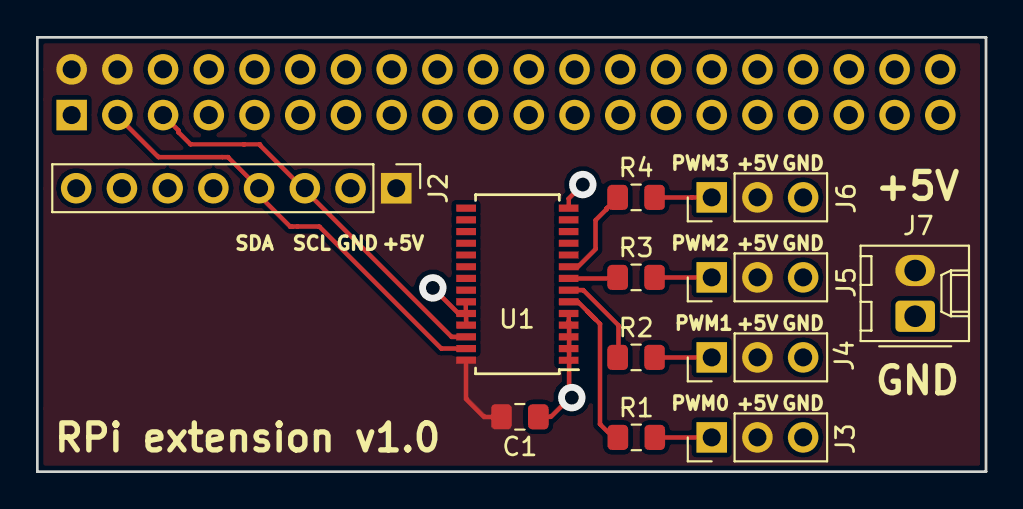
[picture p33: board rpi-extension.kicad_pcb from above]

Board: 2 copper layers, 52.7 x 24.1 mm, 13 parts (1 on the bottom side), 12 nets.

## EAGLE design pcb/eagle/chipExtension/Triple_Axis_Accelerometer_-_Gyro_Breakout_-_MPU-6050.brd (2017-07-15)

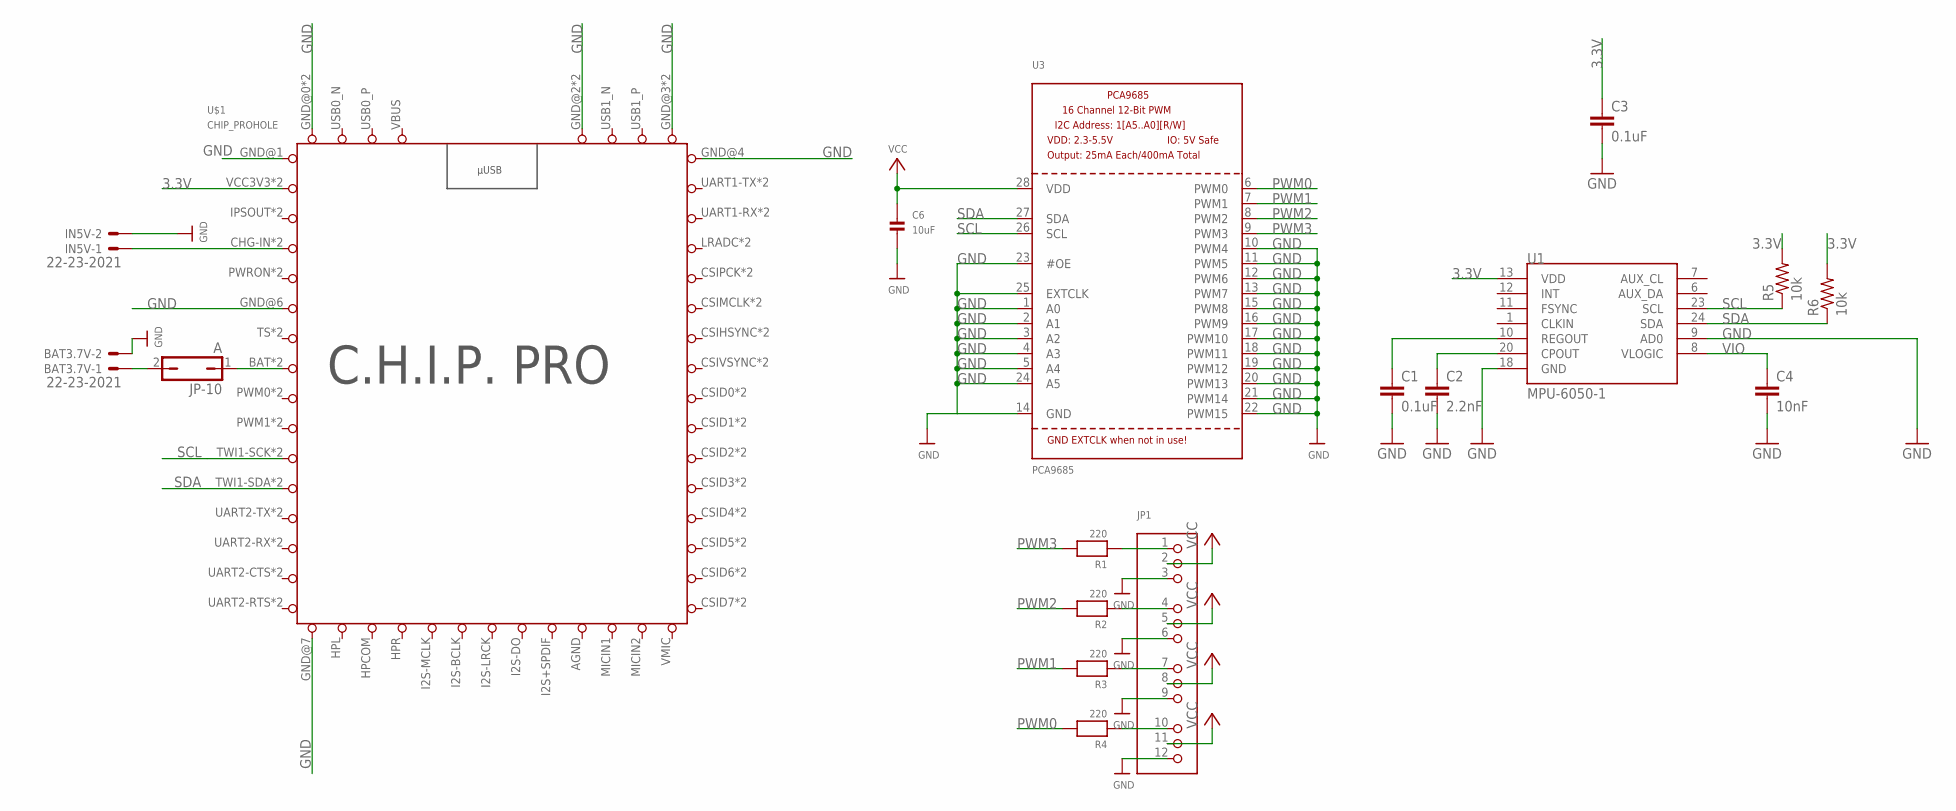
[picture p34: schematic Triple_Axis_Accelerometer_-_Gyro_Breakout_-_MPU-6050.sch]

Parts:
BAT3.7V: 22-23-2021
C1, C3: 0.1uF; 0603-CAP
C2: 2.2nF; 0603-CAP
C4: 10nF; 0603-CAP
C6: 10uF; 0805
IN5V: 22-23-2021
JP1: HEADER-3X04; 3X04
JP-10: A; JP1
R1, R2, R3, R4: 220; 0805
R5, R6: 10k; R0805
U1: MPU-6050-1; QFN-24-4MM2
U3: PCA9685; TSSOP28
U$1: CHIP_PROHOLE; CHIP_PRO_HOLE

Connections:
3.3V: C3.1, R5.2, R6.2, U1.13 (VDD), U$1.VCC3V3, U$1.VCC3V3-1 (VCC3V3)
AGND: U$1.AGND
GND: BAT3.7V.2, C1.2, C2.2, C3.2, C4.2, C6.2, IN5V.2, JP1.3, JP1.6, JP1.9, JP1.12, U1.9 (AD0), U1.18 (GND), U3.1 (A0), U3.2 (A1), U3.3 (A2), U3.4 (A3), U3.5 (A4), U3.10 (PWM4), U3.11 (PWM5), U3.12 (PWM6), U3.13 (PWM7), U3.14 (GND), U3.15 (PWM8), U3.16 (PWM9), U3.17 (PWM10), U3.18 (PWM11), U3.19 (PWM12), U3.20 (PWM13), U3.21 (PWM14), U3.22 (PWM15), U3.23 (#OE), U3.24 (A5), U3.25 (EXTCLK), U$1.GND@0 (GND), U$1.GND@0-1 (GND), U$1.GND@1 (GND), U$1.GND@2 (GND), U$1.GND@2-1 (GND), U$1.GND@3 (GND), U$1.GND@3-1 (GND), U$1.GND@4 (GND), U$1.GND@6 (GND), U$1.GND@7 (GND)
IPSOUT: U$1.IPSOUT, U$1.IPSOUT-1 (IPSOUT)
unnamed: JP1.1, R1.1
unnamed: JP1.4, R2.1
unnamed: C2.1, U1.20 (CPOUT)
unnamed: JP1.7, R3.1
unnamed: C1.1, U1.10 (REGOUT)
unnamed: JP1.10, R4.1
unnamed: IN5V.1, U$1.CHG-IN, U$1.CHG-IN-1 (CHG-IN)
PWM0: R4.2, U3.6 (PWM0)
PWM1: R3.2, U3.7 (PWM1)
PWM2: R2.2, U3.8 (PWM2)
PWM3: R1.2, U3.9 (PWM3)
SCL: R5.1, U1.23 (SCL), U3.26 (SCL), U$1.TWI1-SCK, U$1.TWI1-SCK-1 (TWI1-SCK)
SDA: R6.1, U1.24 (SDA), U3.27 (SDA), U$1.TWI1-SDA, U$1.TWI1-SDA-1 (TWI1-SDA)
VBUS: U$1.VBUS
VCC: BAT3.7V.1, C6.1, JP1.2, JP1.5, JP1.8, JP1.11, JP-10.1, JP-10.2, U3.28 (VDD), U$1.BAT, U$1.BAT-1 (BAT)
VIO: C4.1, U1.8 (VLOGIC)

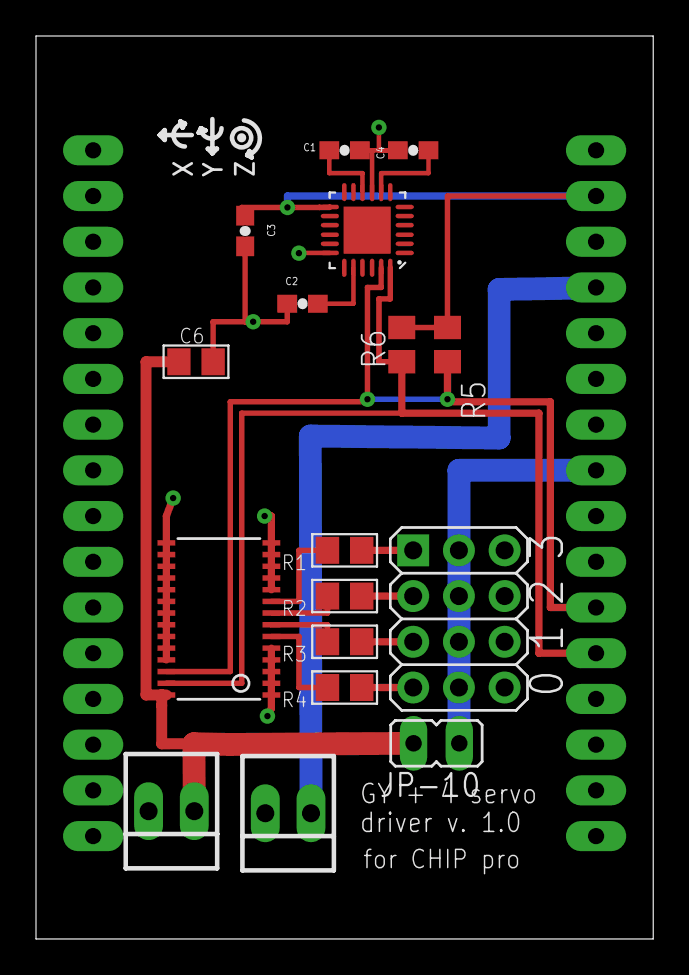
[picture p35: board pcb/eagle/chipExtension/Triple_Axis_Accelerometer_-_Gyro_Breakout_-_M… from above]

Board: 2 copper layers, 34.3 x 50.2 mm, 18 parts (1 on the bottom side), 18 nets.

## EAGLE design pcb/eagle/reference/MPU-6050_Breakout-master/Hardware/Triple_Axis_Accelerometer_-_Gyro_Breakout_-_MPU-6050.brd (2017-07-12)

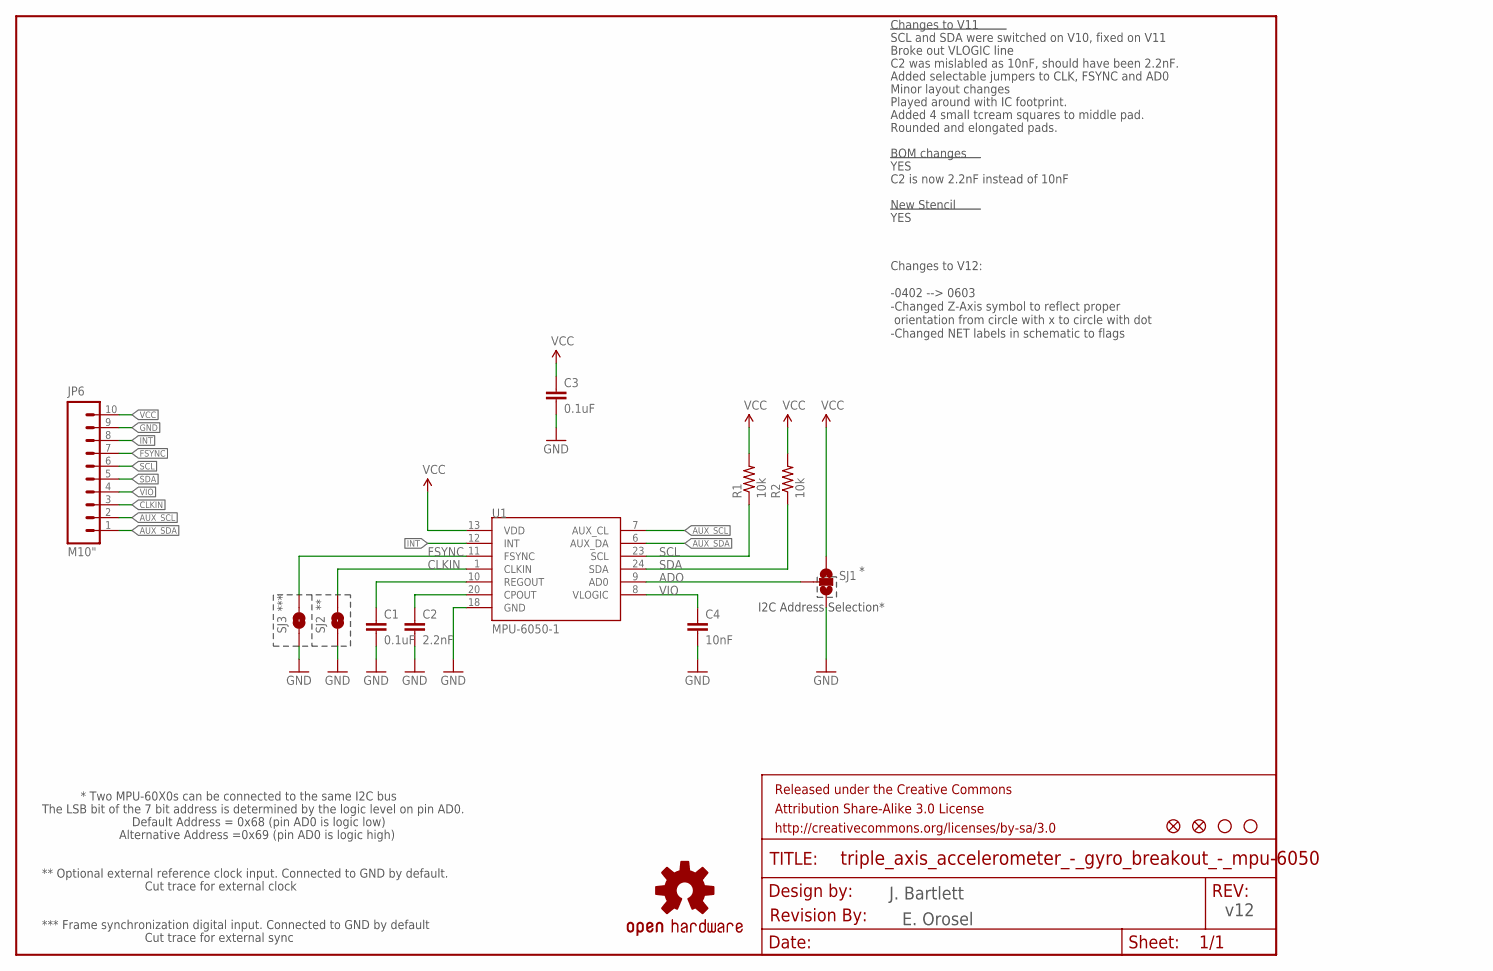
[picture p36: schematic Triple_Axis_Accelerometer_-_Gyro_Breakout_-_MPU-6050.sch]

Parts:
C1, C3: 0.1uF; 0603-CAP
C2: 2.2nF; 0603-CAP
C4: 10nF; 0603-CAP
FRAME1: FRAME-LETTER; CREATIVE_COMMONS
JP2, JP5: FIDUCIALUFIDUCIAL; MICRO-FIDUCIAL
JP3, JP4: STAND-OFFTIGHT; STAND-OFF-TIGHT
JP6: M10"; 1X10
R1, R2: 10k; 0603-RES
SJ1: SOLDERJUMPER_2WAYPASTE2&3; SJ_3_PASTE2&3
SJ2, SJ3: SOLDERJUMPERTRACE; SJ_2S-TRACE
U1: MPU-6050-1; QFN-24-4MM2
U$1: OSHW-LOGOS; OSHW-LOGO-S
U$5: REVISION

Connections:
ADO: SJ1.2, U1.9 (AD0)
AUX_SCL: JP6.2, U1.7 (AUX_CL)
AUX_SDA: JP6.1, U1.6 (AUX_DA)
CLKIN: JP6.3, SJ2.2, U1.1 (CLKIN)
FSYNC: JP6.7, SJ3.2, U1.11 (FSYNC)
GND: C1.2, C2.2, C3.2, C4.2, JP6.9, SJ1.3, SJ2.1, SJ3.1, U1.18 (GND)
INT: JP6.8, U1.12 (INT)
unnamed: C2.1, U1.20 (CPOUT)
unnamed: C1.1, U1.10 (REGOUT)
SCL: JP6.6, R1.1, U1.23 (SCL)
SDA: JP6.5, R2.1, U1.24 (SDA)
VCC: C3.1, JP6.10, R1.2, R2.2, SJ1.1, U1.13 (VDD)
VIO: C4.1, JP6.4, U1.8 (VLOGIC)

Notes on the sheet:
J. Bartlett
I2C Address Selection*
*** Frame synchronization digital input. Connected to GND by default
***
Cut trace for external sync
* Two MPU-60X0s can be connected to the same I2C bus
Default Address = 0x68 (pin AD0 is logic low)
Alternative Address =0x69 (pin AD0 is logic high)
The LSB bit of the 7 bit address is determined by the logic level on pin AD0.
** Optional external reference clock input. Connected to GND by default.
Cut trace for external clock
Changes to V11
SCL and SDA were switched on V10, fixed on V11
C2 was mislabled as 10nF, should have been 2.2nF.
Broke out VLOGIC line
BOM changes
New Stencil
YES
C2 is now 2.2nF instead of 10nF
Minor layout changes
Added selectable jumpers to CLK, FSYNC and AD0
Played around with IC footprint.
Changes to V12: -0402 --> 0603 -Changed Z-Axis symbol to reflect proper orientation from circle with x to circle with dot -Changed NET labels in schematic to flags
E. Orosel
v12
Added 4 small tcream squares to middle pad.
Rounded and elongated pads.

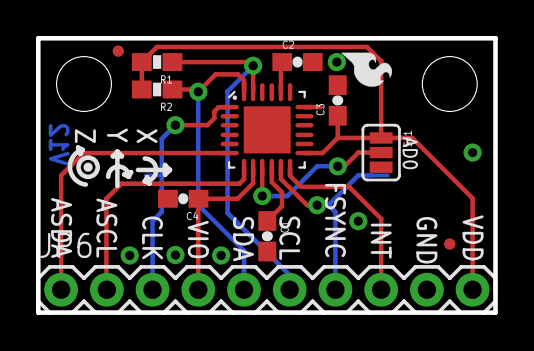
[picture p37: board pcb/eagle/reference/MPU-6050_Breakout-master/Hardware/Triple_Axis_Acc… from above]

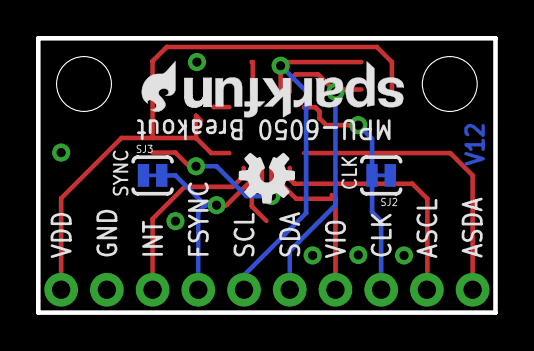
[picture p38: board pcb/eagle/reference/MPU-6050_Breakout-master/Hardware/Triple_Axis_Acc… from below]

Board: 2 copper layers, 25.4 x 15.2 mm, 21 parts (5 on the bottom side), 13 nets.

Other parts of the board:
U$2, U$3: SFE-LOGO-FLAME
U$4: SFE-NEW-WEB

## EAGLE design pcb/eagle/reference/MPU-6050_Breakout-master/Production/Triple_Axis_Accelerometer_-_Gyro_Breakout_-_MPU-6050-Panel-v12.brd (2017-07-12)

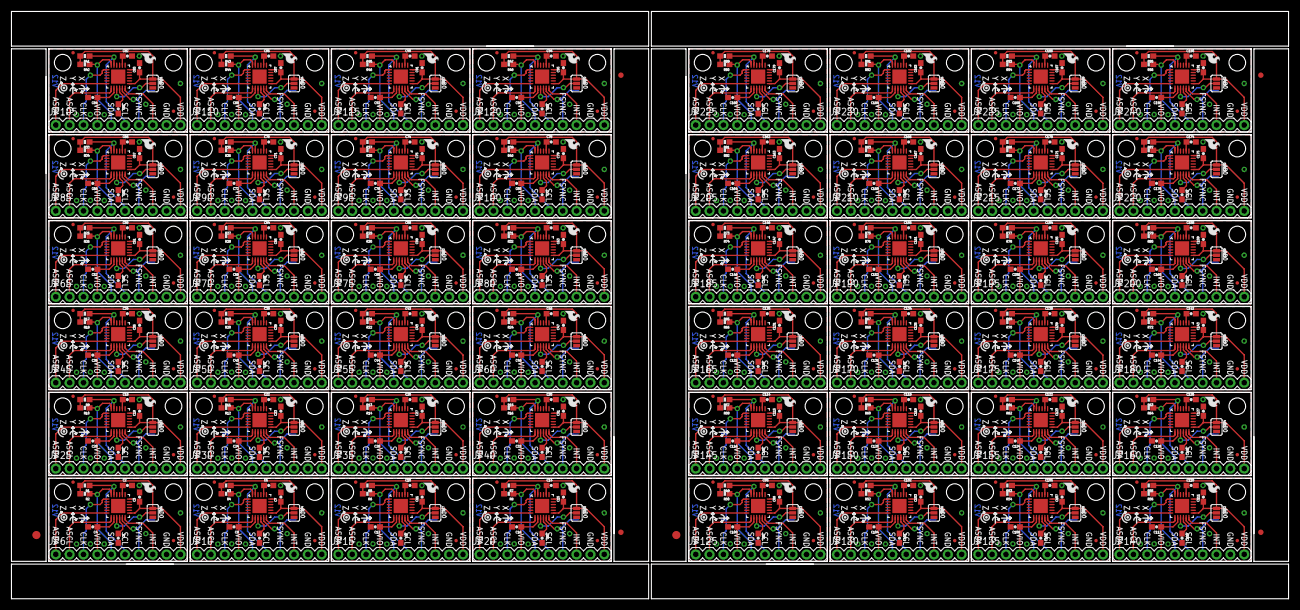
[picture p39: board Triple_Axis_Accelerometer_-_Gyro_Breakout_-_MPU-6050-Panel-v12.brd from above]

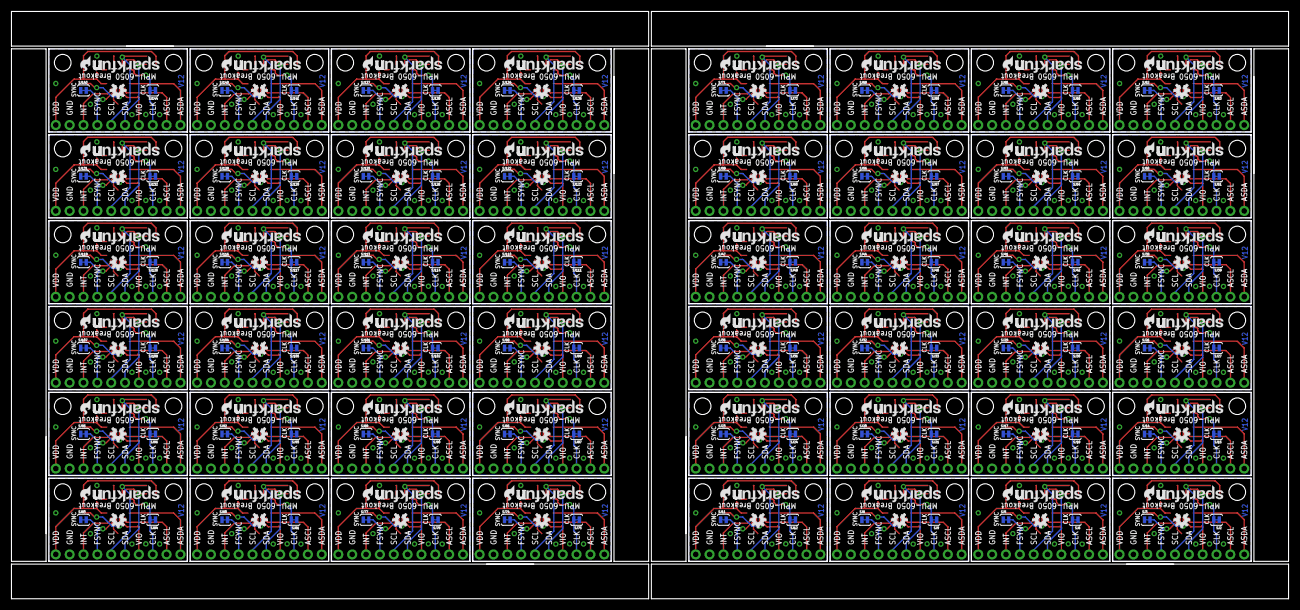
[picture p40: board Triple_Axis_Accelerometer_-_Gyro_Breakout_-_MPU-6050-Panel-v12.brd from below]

Board: 2 copper layers, 234.2 x 107.7 mm, 918 parts (240 on the bottom side), 624 nets.

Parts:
C1, C3, C5, C7, C9, C11, C13, C15, C17, C19, C21, C23, C25, C27, C29, C31, C33, C35, C37, C39, C41, C43, C45, C47, C49, C51, C53, C55, C57, C59, C61, C63, C65, C67, C69, C71, C73, C75, C77, C79, C81, C83, C85, C87, C89, C91, C93, C95, C97, C99, C101, C103, C105, C107, C109, C111, C113, C115, C117, C119, C121, C123, C125, C127, C129, C131, C133, C135, C137, C139, C141, C143, C145, C147, C149, C151, C153, C155, C157, C159, C161, C163, C165, C167, C169, C171, C173, C175, C177, C179, C181, C183, C185, C187, C189, C191: 0.1uF; 0603-CAP
C2, C6, C10, C14, C18, C22, C26, C30, C34, C38, C42, C46, C50, C54, C58, C62, C66, C70, C74, C78, C82, C86, C90, C94, C98, C102, C106, C110, C114, C118, C122, C126, C130, C134, C138, C142, C146, C150, C154, C158, C162, C166, C170, C174, C178, C182, C186, C190: 2.2nF; 0603-CAP
C4, C8, C12, C16, C20, C24, C28, C32, C36, C40, C44, C48, C52, C56, C60, C64, C68, C72, C76, C80, C84, C88, C92, C96, C100, C104, C108, C112, C116, C120, C124, C128, C132, C136, C140, C144, C148, C152, C156, C160, C164, C168, C172, C176, C180, C184, C188, C192: 10nF; 0603-CAP
E$1, E$6: FIDUCIAL-1.5X3
E$2, E$3, E$4, E$5: FIDUCIAL-1X2
JP1, JP3, JP4, JP7, JP11, JP12, JP16, JP17, JP21, JP22, JP26, JP27, JP31, JP32, JP36, JP37, JP41, JP42, JP46, JP47, JP51, JP52, JP56, JP57, JP61, JP62, JP66, JP67, JP71, JP72, JP76, JP77, JP81, JP82, JP86, JP87, JP91, JP92, JP96, JP97, JP101, JP102, JP106, JP107, JP111, JP112, JP116, JP117, JP121, JP122, JP126, JP127, JP131, JP132, JP136, JP137, JP141, JP142, JP146, JP147, JP151, JP152, JP156, JP157, JP161, JP162, JP166, JP167, JP171, JP172, JP176, JP177, JP181, JP182, JP186, JP187, JP191, JP192, JP196, JP197, JP201, JP202, JP206, JP207, JP211, JP212, JP216, JP217, JP221, JP222, JP226, JP227, JP231, JP232, JP236, JP237: STAND-OFFTIGHT; STAND-OFF-TIGHT
JP2, JP5, JP8, JP9, JP13, JP14, JP18, JP19, JP23, JP24, JP28, JP29, JP33, JP34, JP38, JP39, JP43, JP44, JP48, JP49, JP53, JP54, JP58, JP59, JP63, JP64, JP68, JP69, JP73, JP74, JP78, JP79, JP83, JP84, JP88, JP89, JP93, JP94, JP98, JP99, JP103, JP104, JP108, JP109, JP113, JP114, JP118, JP119, JP123, JP124, JP128, JP129, JP133, JP134, JP138, JP139, JP143, JP144, JP148, JP149, JP153, JP154, JP158, JP159, JP163, JP164, JP168, JP169, JP173, JP174, JP178, JP179, JP183, JP184, JP188, JP189, JP193, JP194, JP198, JP199, JP203, JP204, JP208, JP209, JP213, JP214, JP218, JP219, JP223, JP224, JP228, JP229, JP233, JP234, JP238, JP239: FIDUCIALUFIDUCIAL; MICRO-FIDUCIAL
JP6, JP10, JP15, JP20, JP25, JP30, JP35, JP40, JP45, JP50, JP55, JP60, JP65, JP70, JP75, JP80, JP85, JP90, JP95, JP100, JP105, JP110, JP115, JP120, JP125, JP130, JP135, JP140, JP145, JP150, JP155, JP160, JP165, JP170, JP175, JP180, JP185, JP190, JP195, JP200, JP205, JP210, JP215, JP220, JP225, JP230, JP235, JP240: M10"; 1X10
R1, R2, R3, R4, R5, R6, R7, R8, R9, R10, R11, R12, R13, R14, R15, R16, R17, R18, R19, R20, R21, R22, R23, R24, R25, R26, R27, R28, R29, R30, R31, R32, R33, R34, R35, R36, R37, R38, R39, R40, R41, R42, R43, R44, R45, R46, R47, R48, R49, R50, R51, R52, R53, R54, R55, R56, R57, R58, R59, R60, R61, R62, R63, R64, R65, R66, R67, R68, R69, R70, R71, R72, R73, R74, R75, R76, R77, R78, R79, R80, R81, R82, R83, R84, R85, R86, R87, R88, R89, R90, R91, R92, R93, R94, R95, R96: 10k; 0603-RES
SJ1, SJ4, SJ7, SJ10, SJ13, SJ16, SJ19, SJ22, SJ25, SJ28, SJ31, SJ34, SJ37, SJ40, SJ43, SJ46, SJ49, SJ52, SJ55, SJ58, SJ61, SJ64, SJ67, SJ70, SJ73, SJ76, SJ79, SJ82, SJ85, SJ88, SJ91, SJ94, SJ97, SJ100, SJ103, SJ106, SJ109, SJ112, SJ115, SJ118, SJ121, SJ124, SJ127, SJ130, SJ133, SJ136, SJ139, SJ142: SJ_3_PASTE2&3
SJ2, SJ3, SJ5, SJ6, SJ8, SJ9, SJ11, SJ12, SJ14, SJ15, SJ17, SJ18, SJ20, SJ21, SJ23, SJ24, SJ26, SJ27, SJ29, SJ30, SJ32, SJ33, SJ35, SJ36, SJ38, SJ39, SJ41, SJ42, SJ44, SJ45, SJ47, SJ48, SJ50, SJ51, SJ53, SJ54, SJ56, SJ57, SJ59, SJ60, SJ62, SJ63, SJ65, SJ66, SJ68, SJ69, SJ71, SJ72, SJ74, SJ75, SJ77, SJ78, SJ80, SJ81, SJ83, SJ84, SJ86, SJ87, SJ89, SJ90, SJ92, SJ93, SJ95, SJ96, SJ98, SJ99, SJ101, SJ102, SJ104, SJ105, SJ107, SJ108, SJ110, SJ111, SJ113, SJ114, SJ116, SJ117, SJ119, SJ120, SJ122, SJ123, SJ125, SJ126, SJ128, SJ129, SJ131, SJ132, SJ134, SJ135, SJ137, SJ138, SJ140, SJ141, SJ143, SJ144: SJ_2S-TRACE
U1, U2, U3, U4, U5, U6, U7, U8, U9, U10, U11, U12, U13, U14, U15, U16, U17, U18, U19, U20, U21, U22, U23, U24, U25, U26, U27, U28, U29, U30, U31, U32, U33, U34, U35, U36, U37, U38, U39, U40, U41, U42, U43, U44, U45, U46, U47, U48: MPU-6050-1; QFN-24-4MM2
U$1, U$6, U$10, U$14, U$18, U$22, U$26, U$30, U$34, U$38, U$42, U$46, U$50, U$54, U$58, U$62, U$66, U$70, U$74, U$78, U$82, U$86, U$90, U$94, U$98, U$102, U$106, U$110, U$114, U$118, U$122, U$126, U$130, U$134, U$138, U$142, U$146, U$150, U$154, U$158, U$162, U$166, U$170, U$174, U$178, U$182, U$186, U$190: OSHW-LOGOS; OSHW-LOGO-S
U$2, U$3, U$5, U$7, U$9, U$11, U$13, U$15, U$17, U$19, U$21, U$23, U$25, U$27, U$29, U$31, U$33, U$35, U$37, U$39, U$41, U$43, U$45, U$47, U$49, U$51, U$53, U$55, U$57, U$59, U$61, U$63, U$65, U$67, U$69, U$71, U$73, U$75, U$77, U$79, U$81, U$83, U$85, U$87, U$89, U$91, U$93, U$95, U$97, U$99, U$101, U$103, U$105, U$107, U$109, U$111, U$113, U$115, U$117, U$119, U$121, U$123, U$125, U$127, U$129, U$131, U$133, U$135, U$137, U$139, U$141, U$143, U$145, U$147, U$149, U$151, U$153, U$155, U$157, U$159, U$161, U$163, U$165, U$167, U$169, U$171, U$173, U$175, U$177, U$179, U$181, U$183, U$185, U$187, U$189, U$191: SFE-LOGO-FLAME
U$4, U$8, U$12, U$16, U$20, U$24, U$28, U$32, U$36, U$40, U$44, U$48, U$52, U$56, U$60, U$64, U$68, U$72, U$76, U$80, U$84, U$88, U$92, U$96, U$100, U$104, U$108, U$112, U$116, U$120, U$124, U$128, U$132, U$136, U$140, U$144, U$148, U$152, U$156, U$160, U$164, U$168, U$172, U$176, U$180, U$184, U$188, U$192: SFE-NEW-WEB

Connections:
ADO: SJ1.2, U1.9
ADO1: SJ4.2, U2.9
ADO2: SJ7.2, U3.9
ADO3: SJ10.2, U4.9
ADO4: SJ13.2, U5.9
ADO5: SJ16.2, U6.9
ADO6: SJ19.2, U7.9
ADO7: SJ22.2, U8.9
ADO8: SJ25.2, U9.9
ADO9: SJ28.2, U10.9
ADO10: SJ31.2, U11.9
ADO11: SJ34.2, U12.9
ADO12: SJ37.2, U13.9
ADO13: SJ40.2, U14.9
ADO14: SJ43.2, U15.9
ADO15: SJ46.2, U16.9
ADO16: SJ49.2, U17.9
ADO17: SJ52.2, U18.9
ADO18: SJ55.2, U19.9
ADO19: SJ58.2, U20.9
ADO20: SJ61.2, U21.9
ADO21: SJ64.2, U22.9
ADO22: SJ67.2, U23.9
ADO23: SJ70.2, U24.9
ADO24: SJ73.2, U25.9
ADO25: SJ76.2, U26.9
ADO26: SJ79.2, U27.9
ADO27: SJ82.2, U28.9
ADO28: SJ85.2, U29.9
ADO29: SJ88.2, U30.9
ADO30: SJ91.2, U31.9
ADO31: SJ94.2, U32.9
ADO32: SJ97.2, U33.9
ADO33: SJ100.2, U34.9
ADO34: SJ103.2, U35.9
ADO35: SJ106.2, U36.9
ADO36: SJ109.2, U37.9
ADO37: SJ112.2, U38.9
ADO38: SJ115.2, U39.9
ADO39: SJ118.2, U40.9
ADO40: SJ121.2, U41.9
ADO41: SJ124.2, U42.9
ADO42: SJ127.2, U43.9
ADO43: SJ130.2, U44.9
ADO44: SJ133.2, U45.9
ADO45: SJ136.2, U46.9
ADO46: SJ139.2, U47.9
ADO47: SJ142.2, U48.9
AUX_SCL: JP6.2, U1.7
AUX_SCL1: JP10.2, U2.7
AUX_SCL2: JP15.2, U3.7
AUX_SCL3: JP20.2, U4.7
AUX_SCL4: JP25.2, U5.7
AUX_SCL5: JP30.2, U6.7
AUX_SCL6: JP35.2, U7.7
AUX_SCL7: JP40.2, U8.7
AUX_SCL8: JP45.2, U9.7
AUX_SCL9: JP50.2, U10.7
AUX_SCL10: JP55.2, U11.7
AUX_SCL11: JP60.2, U12.7
AUX_SCL12: JP65.2, U13.7
AUX_SCL13: JP70.2, U14.7
AUX_SCL14: JP75.2, U15.7
AUX_SCL15: JP80.2, U16.7
AUX_SCL16: JP85.2, U17.7
AUX_SCL17: JP90.2, U18.7
AUX_SCL18: JP95.2, U19.7
AUX_SCL19: JP100.2, U20.7
AUX_SCL20: JP105.2, U21.7
AUX_SCL21: JP110.2, U22.7
AUX_SCL22: JP115.2, U23.7
AUX_SCL23: JP120.2, U24.7
AUX_SCL24: JP125.2, U25.7
AUX_SCL25: JP130.2, U26.7
AUX_SCL26: JP135.2, U27.7
AUX_SCL27: JP140.2, U28.7
AUX_SCL28: JP145.2, U29.7
AUX_SCL29: JP150.2, U30.7
AUX_SCL30: JP155.2, U31.7
AUX_SCL31: JP160.2, U32.7
AUX_SCL32: JP165.2, U33.7
AUX_SCL33: JP170.2, U34.7
AUX_SCL34: JP175.2, U35.7
AUX_SCL35: JP180.2, U36.7
AUX_SCL36: JP185.2, U37.7
AUX_SCL37: JP190.2, U38.7
AUX_SCL38: JP195.2, U39.7
AUX_SCL39: JP200.2, U40.7
AUX_SCL40: JP205.2, U41.7
AUX_SCL41: JP210.2, U42.7
AUX_SCL42: JP215.2, U43.7
AUX_SCL43: JP220.2, U44.7
AUX_SCL44: JP225.2, U45.7
AUX_SCL45: JP230.2, U46.7
AUX_SCL46: JP235.2, U47.7
AUX_SCL47: JP240.2, U48.7
AUX_SDA: JP6.1, U1.6
AUX_SDA1: JP10.1, U2.6
AUX_SDA2: JP15.1, U3.6
AUX_SDA3: JP20.1, U4.6
AUX_SDA4: JP25.1, U5.6
AUX_SDA5: JP30.1, U6.6
AUX_SDA6: JP35.1, U7.6
AUX_SDA7: JP40.1, U8.6
AUX_SDA8: JP45.1, U9.6
AUX_SDA9: JP50.1, U10.6
AUX_SDA10: JP55.1, U11.6
AUX_SDA11: JP60.1, U12.6
AUX_SDA12: JP65.1, U13.6
AUX_SDA13: JP70.1, U14.6
AUX_SDA14: JP75.1, U15.6
AUX_SDA15: JP80.1, U16.6
AUX_SDA16: JP85.1, U17.6
AUX_SDA17: JP90.1, U18.6
AUX_SDA18: JP95.1, U19.6
AUX_SDA19: JP100.1, U20.6
AUX_SDA20: JP105.1, U21.6
AUX_SDA21: JP110.1, U22.6
AUX_SDA22: JP115.1, U23.6
AUX_SDA23: JP120.1, U24.6
AUX_SDA24: JP125.1, U25.6
AUX_SDA25: JP130.1, U26.6
AUX_SDA26: JP135.1, U27.6
AUX_SDA27: JP140.1, U28.6
AUX_SDA28: JP145.1, U29.6
AUX_SDA29: JP150.1, U30.6
AUX_SDA30: JP155.1, U31.6
AUX_SDA31: JP160.1, U32.6
AUX_SDA32: JP165.1, U33.6
AUX_SDA33: JP170.1, U34.6
AUX_SDA34: JP175.1, U35.6
AUX_SDA35: JP180.1, U36.6
AUX_SDA36: JP185.1, U37.6
AUX_SDA37: JP190.1, U38.6
AUX_SDA38: JP195.1, U39.6
AUX_SDA39: JP200.1, U40.6
AUX_SDA40: JP205.1, U41.6
AUX_SDA41: JP210.1, U42.6
AUX_SDA42: JP215.1, U43.6
AUX_SDA43: JP220.1, U44.6
AUX_SDA44: JP225.1, U45.6
AUX_SDA45: JP230.1, U46.6
AUX_SDA46: JP235.1, U47.6
AUX_SDA47: JP240.1, U48.6
CLKIN: JP6.3, SJ2.2, U1.1
CLKIN1: JP10.3, SJ6.2, U2.1
CLKIN2: JP15.3, SJ9.2, U3.1
CLKIN3: JP20.3, SJ12.2, U4.1
CLKIN4: JP25.3, SJ15.2, U5.1
CLKIN5: JP30.3, SJ18.2, U6.1
CLKIN6: JP35.3, SJ21.2, U7.1
CLKIN7: JP40.3, SJ24.2, U8.1
CLKIN8: JP45.3, SJ27.2, U9.1
CLKIN9: JP50.3, SJ30.2, U10.1
CLKIN10: JP55.3, SJ33.2, U11.1
CLKIN11: JP60.3, SJ36.2, U12.1
CLKIN12: JP65.3, SJ39.2, U13.1
CLKIN13: JP70.3, SJ42.2, U14.1
CLKIN14: JP75.3, SJ45.2, U15.1
CLKIN15: JP80.3, SJ48.2, U16.1
CLKIN16: JP85.3, SJ51.2, U17.1
CLKIN17: JP90.3, SJ54.2, U18.1
CLKIN18: JP95.3, SJ57.2, U19.1
CLKIN19: JP100.3, SJ60.2, U20.1
CLKIN20: JP105.3, SJ63.2, U21.1
CLKIN21: JP110.3, SJ66.2, U22.1
CLKIN22: JP115.3, SJ69.2, U23.1
CLKIN23: JP120.3, SJ72.2, U24.1
CLKIN24: JP125.3, SJ75.2, U25.1
CLKIN25: JP130.3, SJ78.2, U26.1
CLKIN26: JP135.3, SJ81.2, U27.1
CLKIN27: JP140.3, SJ84.2, U28.1
CLKIN28: JP145.3, SJ87.2, U29.1
CLKIN29: JP150.3, SJ90.2, U30.1
CLKIN30: JP155.3, SJ93.2, U31.1
CLKIN31: JP160.3, SJ96.2, U32.1
CLKIN32: JP165.3, SJ99.2, U33.1
CLKIN33: JP170.3, SJ102.2, U34.1
CLKIN34: JP175.3, SJ105.2, U35.1
CLKIN35: JP180.3, SJ108.2, U36.1
CLKIN36: JP185.3, SJ111.2, U37.1
CLKIN37: JP190.3, SJ114.2, U38.1
CLKIN38: JP195.3, SJ117.2, U39.1
CLKIN39: JP200.3, SJ120.2, U40.1
CLKIN40: JP205.3, SJ123.2, U41.1
CLKIN41: JP210.3, SJ126.2, U42.1
CLKIN42: JP215.3, SJ129.2, U43.1
CLKIN43: JP220.3, SJ132.2, U44.1
CLKIN44: JP225.3, SJ135.2, U45.1
CLKIN45: JP230.3, SJ138.2, U46.1
CLKIN46: JP235.3, SJ141.2, U47.1
CLKIN47: JP240.3, SJ144.2, U48.1
FSYNC: JP6.7, SJ3.2, U1.11
FSYNC1: JP10.7, SJ5.2, U2.11
FSYNC2: JP15.7, SJ8.2, U3.11
FSYNC3: JP20.7, SJ11.2, U4.11
FSYNC4: JP25.7, SJ14.2, U5.11
FSYNC5: JP30.7, SJ17.2, U6.11
FSYNC6: JP35.7, SJ20.2, U7.11
FSYNC7: JP40.7, SJ23.2, U8.11
FSYNC8: JP45.7, SJ26.2, U9.11
FSYNC9: JP50.7, SJ29.2, U10.11
FSYNC10: JP55.7, SJ32.2, U11.11
FSYNC11: JP60.7, SJ35.2, U12.11
FSYNC12: JP65.7, SJ38.2, U13.11
FSYNC13: JP70.7, SJ41.2, U14.11
FSYNC14: JP75.7, SJ44.2, U15.11
FSYNC15: JP80.7, SJ47.2, U16.11
FSYNC16: JP85.7, SJ50.2, U17.11
FSYNC17: JP90.7, SJ53.2, U18.11
FSYNC18: JP95.7, SJ56.2, U19.11
FSYNC19: JP100.7, SJ59.2, U20.11
FSYNC20: JP105.7, SJ62.2, U21.11
FSYNC21: JP110.7, SJ65.2, U22.11
FSYNC22: JP115.7, SJ68.2, U23.11
FSYNC23: JP120.7, SJ71.2, U24.11
FSYNC24: JP125.7, SJ74.2, U25.11
FSYNC25: JP130.7, SJ77.2, U26.11
FSYNC26: JP135.7, SJ80.2, U27.11
FSYNC27: JP140.7, SJ83.2, U28.11
FSYNC28: JP145.7, SJ86.2, U29.11
FSYNC29: JP150.7, SJ89.2, U30.11
FSYNC30: JP155.7, SJ92.2, U31.11
FSYNC31: JP160.7, SJ95.2, U32.11
FSYNC32: JP165.7, SJ98.2, U33.11
FSYNC33: JP170.7, SJ101.2, U34.11
FSYNC34: JP175.7, SJ104.2, U35.11
FSYNC35: JP180.7, SJ107.2, U36.11
FSYNC36: JP185.7, SJ110.2, U37.11
FSYNC37: JP190.7, SJ113.2, U38.11
FSYNC38: JP195.7, SJ116.2, U39.11
FSYNC39: JP200.7, SJ119.2, U40.11
FSYNC40: JP205.7, SJ122.2, U41.11
FSYNC41: JP210.7, SJ125.2, U42.11
FSYNC42: JP215.7, SJ128.2, U43.11
FSYNC43: JP220.7, SJ131.2, U44.11
FSYNC44: JP225.7, SJ134.2, U45.11
FSYNC45: JP230.7, SJ137.2, U46.11
FSYNC46: JP235.7, SJ140.2, U47.11
FSYNC47: JP240.7, SJ143.2, U48.11
GND: C1.2, C2.2, C3.2, C4.2, JP6.9, SJ1.3, SJ2.1, SJ3.1, U1.18
GND1: C5.2, C6.2, C7.2, C8.2, JP10.9, SJ4.3, SJ5.1, SJ6.1, U2.18
GND2: C9.2, C10.2, C11.2, C12.2, JP15.9, SJ7.3, SJ8.1, SJ9.1, U3.18
GND3: C13.2, C14.2, C15.2, C16.2, JP20.9, SJ10.3, SJ11.1, SJ12.1, U4.18
GND4: C17.2, C18.2, C19.2, C20.2, JP25.9, SJ13.3, SJ14.1, SJ15.1, U5.18
GND5: C21.2, C22.2, C23.2, C24.2, JP30.9, SJ16.3, SJ17.1, SJ18.1, U6.18
GND6: C25.2, C26.2, C27.2, C28.2, JP35.9, SJ19.3, SJ20.1, SJ21.1, U7.18
GND7: C29.2, C30.2, C31.2, C32.2, JP40.9, SJ22.3, SJ23.1, SJ24.1, U8.18
GND8: C33.2, C34.2, C35.2, C36.2, JP45.9, SJ25.3, SJ26.1, SJ27.1, U9.18
GND9: C37.2, C38.2, C39.2, C40.2, JP50.9, SJ28.3, SJ29.1, SJ30.1, U10.18
GND10: C41.2, C42.2, C43.2, C44.2, JP55.9, SJ31.3, SJ32.1, SJ33.1, U11.18
GND11: C45.2, C46.2, C47.2, C48.2, JP60.9, SJ34.3, SJ35.1, SJ36.1, U12.18
GND12: C49.2, C50.2, C51.2, C52.2, JP65.9, SJ37.3, SJ38.1, SJ39.1, U13.18
GND13: C53.2, C54.2, C55.2, C56.2, JP70.9, SJ40.3, SJ41.1, SJ42.1, U14.18
GND14: C57.2, C58.2, C59.2, C60.2, JP75.9, SJ43.3, SJ44.1, SJ45.1, U15.18
GND15: C61.2, C62.2, C63.2, C64.2, JP80.9, SJ46.3, SJ47.1, SJ48.1, U16.18
GND16: C65.2, C66.2, C67.2, C68.2, JP85.9, SJ49.3, SJ50.1, SJ51.1, U17.18
GND17: C69.2, C70.2, C71.2, C72.2, JP90.9, SJ52.3, SJ53.1, SJ54.1, U18.18
GND18: C73.2, C74.2, C75.2, C76.2, JP95.9, SJ55.3, SJ56.1, SJ57.1, U19.18
GND19: C77.2, C78.2, C79.2, C80.2, JP100.9, SJ58.3, SJ59.1, SJ60.1, U20.18
GND20: C81.2, C82.2, C83.2, C84.2, JP105.9, SJ61.3, SJ62.1, SJ63.1, U21.18
GND21: C85.2, C86.2, C87.2, C88.2, JP110.9, SJ64.3, SJ65.1, SJ66.1, U22.18
GND22: C89.2, C90.2, C91.2, C92.2, JP115.9, SJ67.3, SJ68.1, SJ69.1, U23.18
GND23: C93.2, C94.2, C95.2, C96.2, JP120.9, SJ70.3, SJ71.1, SJ72.1, U24.18
GND24: C97.2, C98.2, C99.2, C100.2, JP125.9, SJ73.3, SJ74.1, SJ75.1, U25.18
GND25: C101.2, C102.2, C103.2, C104.2, JP130.9, SJ76.3, SJ77.1, SJ78.1, U26.18
GND26: C105.2, C106.2, C107.2, C108.2, JP135.9, SJ79.3, SJ80.1, SJ81.1, U27.18
GND27: C109.2, C110.2, C111.2, C112.2, JP140.9, SJ82.3, SJ83.1, SJ84.1, U28.18
GND28: C113.2, C114.2, C115.2, C116.2, JP145.9, SJ85.3, SJ86.1, SJ87.1, U29.18
GND29: C117.2, C118.2, C119.2, C120.2, JP150.9, SJ88.3, SJ89.1, SJ90.1, U30.18
GND30: C121.2, C122.2, C123.2, C124.2, JP155.9, SJ91.3, SJ92.1, SJ93.1, U31.18
GND31: C125.2, C126.2, C127.2, C128.2, JP160.9, SJ94.3, SJ95.1, SJ96.1, U32.18
GND32: C129.2, C130.2, C131.2, C132.2, JP165.9, SJ97.3, SJ98.1, SJ99.1, U33.18
GND33: C133.2, C134.2, C135.2, C136.2, JP170.9, SJ100.3, SJ101.1, SJ102.1, U34.18
GND34: C137.2, C138.2, C139.2, C140.2, JP175.9, SJ103.3, SJ104.1, SJ105.1, U35.18
GND35: C141.2, C142.2, C143.2, C144.2, JP180.9, SJ106.3, SJ107.1, SJ108.1, U36.18
GND36: C145.2, C146.2, C147.2, C148.2, JP185.9, SJ109.3, SJ110.1, SJ111.1, U37.18
GND37: C149.2, C150.2, C151.2, C152.2, JP190.9, SJ112.3, SJ113.1, SJ114.1, U38.18
GND38: C153.2, C154.2, C155.2, C156.2, JP195.9, SJ115.3, SJ116.1, SJ117.1, U39.18
GND39: C157.2, C158.2, C159.2, C160.2, JP200.9, SJ118.3, SJ119.1, SJ120.1, U40.18
GND40: C161.2, C162.2, C163.2, C164.2, JP205.9, SJ121.3, SJ122.1, SJ123.1, U41.18
GND41: C165.2, C166.2, C167.2, C168.2, JP210.9, SJ124.3, SJ125.1, SJ126.1, U42.18
GND42: C169.2, C170.2, C171.2, C172.2, JP215.9, SJ127.3, SJ128.1, SJ129.1, U43.18
GND43: C173.2, C174.2, C175.2, C176.2, JP220.9, SJ130.3, SJ131.1, SJ132.1, U44.18
GND44: C177.2, C178.2, C179.2, C180.2, JP225.9, SJ133.3, SJ134.1, SJ135.1, U45.18
GND45: C181.2, C182.2, C183.2, C184.2, JP230.9, SJ136.3, SJ137.1, SJ138.1, U46.18
GND46: C185.2, C186.2, C187.2, C188.2, JP235.9, SJ139.3, SJ140.1, SJ141.1, U47.18
GND47: C189.2, C190.2, C191.2, C192.2, JP240.9, SJ142.3, SJ143.1, SJ144.1, U48.18
INT: JP6.8, U1.12
INT1: JP10.8, U2.12
INT2: JP15.8, U3.12
INT3: JP20.8, U4.12
INT4: JP25.8, U5.12
INT5: JP30.8, U6.12
INT6: JP35.8, U7.12
INT7: JP40.8, U8.12
INT8: JP45.8, U9.12
INT9: JP50.8, U10.12
INT10: JP55.8, U11.12
INT11: JP60.8, U12.12
INT12: JP65.8, U13.12
INT13: JP70.8, U14.12
INT14: JP75.8, U15.12
INT15: JP80.8, U16.12
INT16: JP85.8, U17.12
INT17: JP90.8, U18.12
INT18: JP95.8, U19.12
INT19: JP100.8, U20.12
INT20: JP105.8, U21.12
INT21: JP110.8, U22.12
INT22: JP115.8, U23.12
INT23: JP120.8, U24.12
INT24: JP125.8, U25.12
INT25: JP130.8, U26.12
INT26: JP135.8, U27.12
INT27: JP140.8, U28.12
INT28: JP145.8, U29.12
INT29: JP150.8, U30.12
INT30: JP155.8, U31.12
INT31: JP160.8, U32.12
INT32: JP165.8, U33.12
INT33: JP170.8, U34.12
INT34: JP175.8, U35.12
INT35: JP180.8, U36.12
INT36: JP185.8, U37.12
INT37: JP190.8, U38.12
INT38: JP195.8, U39.12
INT39: JP200.8, U40.12
INT40: JP205.8, U41.12
INT41: JP210.8, U42.12
INT42: JP215.8, U43.12
INT43: JP220.8, U44.12
INT44: JP225.8, U45.12
INT45: JP230.8, U46.12
INT46: JP235.8, U47.12
INT47: JP240.8, U48.12
unnamed: C6.1, U2.20
unnamed: C5.1, U2.10
unnamed: C2.1, U1.20
unnamed: C10.1, U3.20
unnamed: C1.1, U1.10
unnamed: C9.1, U3.10
unnamed: C14.1, U4.20
unnamed: C13.1, U4.10
unnamed: C18.1, U5.20
unnamed: C17.1, U5.10
unnamed: C22.1, U6.20
unnamed: C21.1, U6.10
unnamed: C26.1, U7.20
unnamed: C25.1, U7.10
unnamed: C30.1, U8.20
unnamed: C29.1, U8.10
unnamed: C34.1, U9.20
unnamed: C33.1, U9.10
unnamed: C38.1, U10.20
unnamed: C37.1, U10.10
unnamed: C42.1, U11.20
unnamed: C41.1, U11.10
unnamed: C46.1, U12.20
unnamed: C45.1, U12.10
unnamed: C50.1, U13.20
unnamed: C49.1, U13.10
unnamed: C54.1, U14.20
unnamed: C53.1, U14.10
unnamed: C58.1, U15.20
unnamed: C57.1, U15.10
unnamed: C62.1, U16.20
unnamed: C61.1, U16.10
unnamed: C66.1, U17.20
unnamed: C65.1, U17.10
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

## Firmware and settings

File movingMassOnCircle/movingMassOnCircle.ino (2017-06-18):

#include <Servo.h>

Servo servo1;
Servo servo2;
Servo servo3;
byte angles[] = {0, 1, 2, 3, 4, 5, 6, 7, 8, 9, 10, 11, 12, 13, 14, 15, 16, 17, 18, 19, 20, 21, 22, 23, 24, 25, 26, 27, 28, 29, 30, 31, 32, 33, 34, 35, 36, 37, 38, 39, 40, 41, 42, 43, 44, 45, 46, 47, 48, 49, 50, 51, 52, 53, 54, 55, 56, 57, 58, 59, 60, 61, 62, 63, 64, 65, 66, 67, 68, 69, 70, 71, 72, 73, 74, 75, 76, 77, 78, 79, 80, 81, 82, 83, 84, 85, 86, 87, 88, 89, 90, 91, 92, 93, 94, 95, 96, 97, 98, 99, 100, 101, 102, 103, 104, 105, 106, 107, 108, 109, 110, 111, 112, 113, 114, 115, 116, 117, 118, 119, 120, 121, 122, 123, 124, 125, 126, 127, 128, 129, 130, 131, 132, 133, 134, 135, 136, 137, 138, 139, 140, 141, 142, 143, 144, 145, 146, 147, 148, 149, 150, 151, 152, 153, 154, 155, 156, 157, 158, 159, 160, 161, 162, 163, 164, 165, 166, 167, 168, 169, 170, 171, 172, 173, 174, 175, 176, 177, 178, 179, 180, 179, 179, 178, 177, 177, 176, 175, 175, 174, 173, 172, 172, 171, 170, 170, 169, 168, 168, 167, 166, 166, 165, 164, 163, 163, 162, 161, 161, 160, 159, 158, 158, 157, 156, 156, 155, 154, 153, 153, 152, 151, 151, 150, 149, 148, 148, 147, 146, 145, 145, 144, 143, 142, 142, 141, 140, 139, 138, 138, 137, 136, 135, 134, 134, 133, 132, 131, 130, 130, 129, 128, 127, 126, 125, 125, 124, 123, 122, 121, 120, 119, 118, 118, 117, 116, 115, 114, 113, 112, 111, 110, 109, 108, 107, 106, 105, 105, 104, 103, 102, 101, 100, 99, 98, 96, 95, 94, 93, 92, 91, 90, 89, 88, 87, 86, 85, 84, 83, 81, 80, 79, 78, 77, 76, 74, 73, 72, 71, 70, 68, 67, 66, 65, 64, 62, 61, 60, 59, 57, 56, 55, 53, 52, 51, 49, 48, 47, 45, 44, 43, 41, 40, 39, 37, 36, 34, 33, 32, 30, 29, 27, 26, 25, 23, 22, 20, 19, 17, 16, 15, 13, 12, 10, 9, 7, 6, 4, 3, 1
  };
  
int nbAngles = sizeof(angles);


void setup (){
  servo1.attach(A0);
  servo2.attach(A1);
  servo3.attach(A2);
}

int counter = 0;

void loop () {
  servo1.write(angles[counter]);
  servo2.write(angles[(counter + nbAngles / 3) % nbAngles]);
  servo3.write(angles[(counter + nbAngles / 3 * 2) % nbAngles]);
  
  counter++;
  if (counter==nbAngles) counter=0;
  delay(10                                                                                     );

}

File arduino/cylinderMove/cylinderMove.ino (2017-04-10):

#include <Servo.h> //import servo library

Servo servo1;//defining the first servo 're gonna use
Servo servo2;
Servo servo3;

int pos = 10; //servo1 initial position

int servoDelay = 100; //time you wait between every actions the servo does

int currentDirection=1;
int angle1=90;

void setup()
{
  servo1.attach( A1 ); //defining wich pin is controlling the servo
  servo1.write(pos);

  servo2.attach(A2 );
  servo2.write(pos);

  servo3.attach( A0 );
  servo3.write(pos);



}



void loop() {
  while(true) {
    angle1+=currentDirection;
    if (angle1>170 || angle1<90) {
      currentDirection*=-1;
    } 
    else {
    servo1.write(pos);
    }
    servo1.write(angle1);
   
    delay(servoDelay);
  }

}

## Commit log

2016-10-17 Datasheet MPU-6050 accelerometer - gyroscope
2016-10-17 Add initial freecad files
    [Wheel.fcstd, model-board.fcstd, model-cylinder.fcstd]
2016-10-17 Add servo oscilloscope
2016-11-28 reorganising directories
    [Wheel.fcstd, model-board.fcstd, model-cylinder.fcstd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]
2016-12-19 Ordering directories
    [mass.fcstd]
2017-01-18 modifing freecad document: wheel
2017-01-21 adding cylinder schemes in pictures
2017-01-29 modifing wheel and wheelAccessory (freecad)
    [Wheel.dxf, Wheel.fcstd, WheelAccessory.fcstd]
2017-02-11 Remove unused files
    [wheelBase (1).FCStd, wheelBase (2).FCStd]
2017-04-03 Adding new geogebra file. This is a first test of sovling the angles of the servo depending on the mass position, graphicaly.
2017-04-05 Working on servosMovement
2017-04-05 Developing servos angles depending on position of the mass
2017-04-08 First working moving servos
2017-04-10 Evolving servoMovement and adding pictures
    [modelCylinder3.FCStd]
2017-04-10 Finally finding the limitation of the servo axis length!
2017-06-19 Adding pictures of prototype2 and upgrading calculusScheme.key.
2017-07-06 Modifing cylinderDataKeynote.
2017-07-12 Working on eagle.
    [Adafruit PCA9685.brd, Adafruit PCA9685.sch, Triple_Axis_Accelerometer_-_Gyro_Breakout_-_MPU-6050-Panel-v12.brd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]
2017-07-13 Adding holes to the PCB on eagle and enhancing the freeca model of cylinder prototype 3.
    [Triple_Axis_Accelerometer_-_Gyro_Breakout_-_MPU-6050.brd, Triple_Axis_Accelerometer_-_Gyro_Breakout_-_MPU-6050.sch, cylinderBackFace.fcstd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]
2017-07-14 Adding jumper to eagle files and enhancing the freecad model of cylinderPrototype3.
    [Triple_Axis_Accelerometer_-_Gyro_Breakout_-_MPU-6050.brd, Triple_Axis_Accelerometer_-_Gyro_Breakout_-_MPU-6050.sch, cylinderBackFace.fcstd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]
2017-07-15 improve eagle design
    [Triple_Axis_Accelerometer_-_Gyro_Breakout_-_MPU-6050.brd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]
2017-07-21 adapt the commandLineFunctions to cylinderPrototype3
    [spiro.dxf]
2017-07-23 modify cylinderDataKeynote
2017-08-18 add the keynote related to the pcb
2017-10-08 clean freecad
    [WheelAccessory.fcstd, cylinder.fcstd, cylinderBackFace.fcstd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]
2017-10-09 add all export files from freecad
    [Wheel.fcstd, servoAxis.fcstd]
2017-10-10 add pdfs of freecad files, add laserCutter keynote
2017-10-16 mainly modify with keynote exports
    [test.FCStd]
2019-03-02 add kicad of rpi extension
    [rpi-extension.kicad_pcb, rpi-extension.sch]
2019-03-03 add kicad extension
    [rpi-extension-B.Cu.gbl, rpi-extension-B.Cu.gbr, rpi-extension-B.Mask.gbr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]
2019-03-10 update kicad for extension
    [rpi-extension.kicad_pcb]
2019-03-10 remove gerber files
    [rpi-extension-B.Cu.gbr, rpi-extension-B.Mask.gbr, rpi-extension-B.Paste.gbr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]
2019-03-13 rearrange repo and work on README
    [Adafruit PCA9685.brd, Adafruit PCA9685.sch, Triple_Axis_Accelerometer_-_Gyro_Breakout_-_MPU-6050-Panel-v12.brd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]
2019-03-15 remove useless files
    [Adafruit PCA9685.brd, Adafruit PCA9685.sch, Triple_Axis_Accelerometer_-_Gyro_Breakout_-_MPU-6050-Panel-v12.brd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]
2019-04-17 enhance raspberry doc
2019-09-06 Update and rename cylinderPrototype3F.svg to cylinderPrototype3F.dxf
    [cylinderPrototype3F.dxf]
2019-09-06 Add files via upload
    svg and dxf files of cp3
    [cylinderPrototype3B.dxf]

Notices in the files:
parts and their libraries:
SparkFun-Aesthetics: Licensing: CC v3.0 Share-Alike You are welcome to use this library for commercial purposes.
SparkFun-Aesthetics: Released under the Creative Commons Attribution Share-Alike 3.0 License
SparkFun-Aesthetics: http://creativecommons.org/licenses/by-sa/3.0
